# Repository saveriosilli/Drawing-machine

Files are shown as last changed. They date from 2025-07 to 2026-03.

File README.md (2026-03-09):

# Drawing Machine

This machine was designed in Fablab O Shanghai as an education project for a class called "Planet Art". The course's aim is to assemble the frame of the machine and re-design some of the structure starting from the provided design \(mainly for the laser cut plates and 3d printed accessories\) and use the machine to experience 2d/3d graphic original creations, self-expression through artwork, machine control electronics and software. After the assembly, test and familiarization with a working machine, students create artworks exploring the many possibilities of human-machine co-creation. The structure and parts of the machine is the result of many iterations and the sum of the improved design from instructors and students.

https://github.com/user-attachments/assets/3ad980b2-f0f4-412e-b6a9-14be8d8319f2

## Images

We are in the process of designing an assembly guide. Meanwhile you can refer to some images and videos to understand how the machine is assembled. Simple clue: the process is pretty easy and straightforward :\)

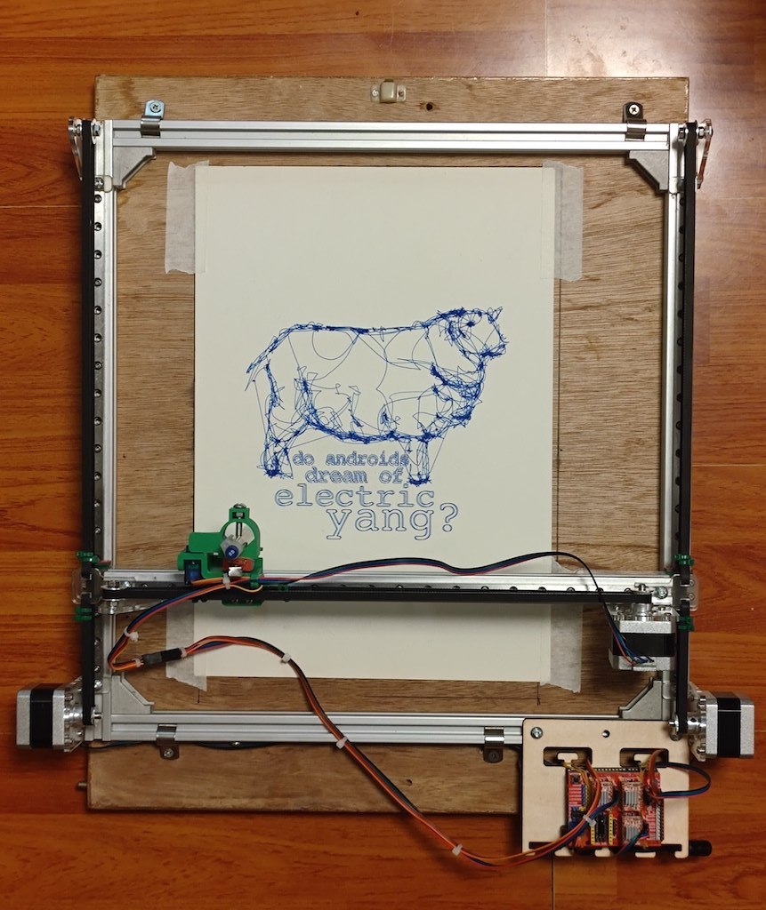
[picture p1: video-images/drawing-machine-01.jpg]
drawing machine 01


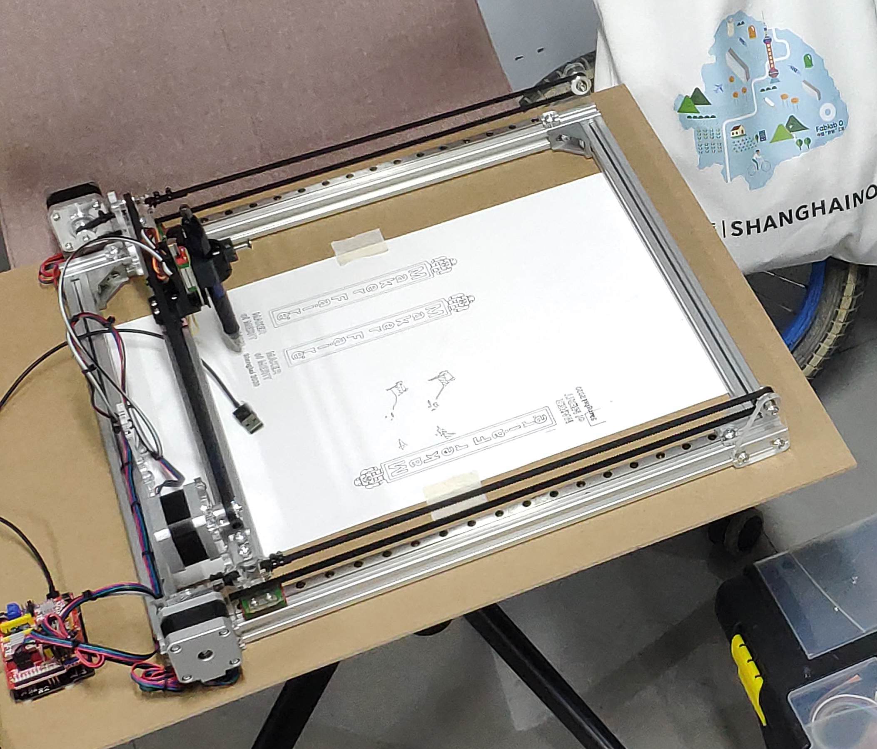
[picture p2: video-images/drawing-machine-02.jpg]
drawing machine 01


## A little history

The  structure of the machine is based on a design by **Daniele Ingrassia @satsha** for a basic machine frame to be assembled in a short workshop he gave at the **STEAM Education International Symposium of Shanghai** in 2019 organised by Fablab O Shanghai and Tongji University College of Design and Innovation. His clever and simple structure using only 20x20 aluminum frames, angle joints, t-nuts, linear guides and two laser cut parts, became part of  Fablab O Shanghai inventory and Saverio Silli @saverio used it as the base for this drawing machine.

## Highlights of this design

The machine has some notable characteristics worth mentioning:

* it can be assembled by a couple of 10 years old in less than two hours
* the 3d printed parts can be printed while assembling the structure and are ready to use when the structure is assembled
* laser cutting takes less than 5 minutes
* only a few common tools are required to assemble the structure
* the size of the machine can be customised
* pen lift is virtually free of any wobbling and can accept several types of pens and other drawing media or be customised to accept different tools

[Find all the Design files in this page](design-files/README.md)

## Machine Control

Aside from the design of the machine structure, a thorough work has been done to polish and troubleshoot the code and workflow to ensure the software installation and operation to be as straightforward as possible. A modified GRBL for Servo library is provided, and several tips are listed covering the most common solutions for a successful operation.

[Find more info on the Electronic system in this page](electronics/README.md)

The machine uses an Arduino Uno with CNC Shield and A4988 Stepper drivers with GRBL for Servo firmware. We suggest to operate the machine through Inventables' Easel.

## Bill of Materials

[Find all the BOM in this page](Material List 2022.pdf)

The material list provides links on Taobao to buy the materials and a description about the materials. For more details you can check the taobao link.

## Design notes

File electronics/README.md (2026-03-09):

# Electronics

We have included a modified and ready to use GRBL for Servo library. To install, first make sure there are no previous installation of any other GRBL libraries in your Arduino libraries folder, then just unzip and copy paste the provided folder in the Arduino Libraries folder.

Restart Arduino software and open the GRBL Upload example in the examples menu, upload the program to your Arduino Uno and the installation is complete.

## Connections

Your Arduino should be equipped with a CNC shield. Make sure the shield has:

1. all 3 jumpers under the drivers for microstepping

2. two jumpers on the Y axis duplication

3. servo motor connected as follow: brown wire \(GND\) to any GND pin on the shield, red wire \(VCC\) to any 5V pin on the shield, orange wire \(signal\) to "Endstop Z-" pin on the shield.

4. 12 Volts and 5 Amps power supply connected to the power supply connector of the CNC shield

5. Stepper motors correctly connected to the 4 pins connector next to the driver \(if motor rotate in the wrong direction, just reverse the connector

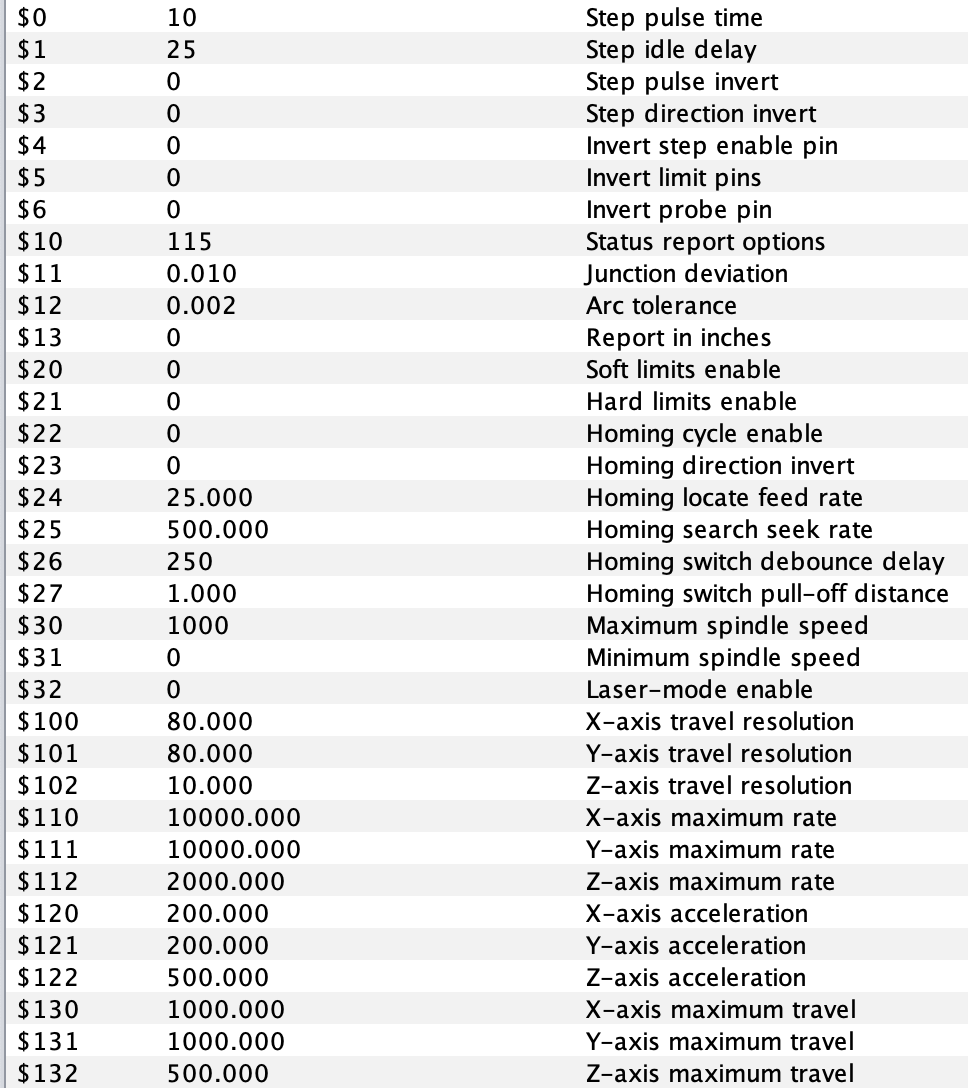
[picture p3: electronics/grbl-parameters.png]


## Notes on the servo motor operation

The basic GRBL firmware is normally controlling a _stepper_ motor to move the Z axis. This modified version make use of a _servo_ motor instead to lift the pen up and down. A normal stepper motor is controlled with coordinates coming from the G-code and its movement is expressed in millimetres  or inches. With a stepper motor you can control exactly the linear movement of the Z axis below and above the zero.

Using a **servo motor** you can only move the Z axis in two pre-defined positions: _Up \(or above the origin\) and Down \(or below the origin\)_.

Using your preferred control software \(Universal G-code Sender, Easel, eCNC to cite a few\) you will have the option to move the Z axis up and down for the length you desire, but with this modified GRBL for Servo firmware you will notice that the servo motor will only move when the machine coordinates actually pass the origin.

If your Z axis position is currently at 0mm \(the origin point\) and you move the Z axis up for 5mm, the Z axis new position will be + 5mm, _but your servo motor will not move_.

Likely, if your Z axis position is currently + 5mm and you move the Z axis down for 5mm, the Z axis new position will be 0, _but your servo motor will not move as well._

In both cases, the Z axis position was equal or bigger than zero.

On the other hand, if your Z axis position is currently at + 5mm and you move the Z axis down for 10mm, the Z axis new position will be -5mm, _and your servo motor will move once_.

**The reason is that the servo motor will only move when the Z axis position passes the origin point.** As long as it passes through the origin you will have your servo motor moving up \(from any point below 0 to any point above 0\) or moving down \(from any point above 0 to any point below 0\).

This is very important because you might find yourself clicking the Z axis movement up and down arrow several time without noticing any movement and you might believe it is a hardware problem. Instead, make sure the movements are always crossing above and below the origin point.

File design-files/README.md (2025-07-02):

# Design Files

The files included are:

1. Laser cut plates, we suggest to use 5mm acrylic. The thickness must be chosen in relation to the lenght of the screw used with t-nuts for assembly, if the thickness is too thin and the screws are too long, the screws will touch the internal channel of the aluminum frame and the plates will not be locked in place.

2. 3D printed pen lift. It is designed to use a small section of linear guide and standard slider, it can mount a standard 9g Servo Motor and it must be equipped with a rubber band to act as a spring that pushes the pen down.

3. The pen holding ring is large enough for several size of pens and markers.

4. The 3D printed parts do not require any support or brim for printing.

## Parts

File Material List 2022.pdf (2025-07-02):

1 | kits. | Kit for total
machines
NAME | TYPE | SIZE | NOTES | QUANTITY /
| | | | 1 MACHINE | QUANTITY
| | | | | / TOTAL | TAOBAO
Linear Guide / 直线导轨滑块线轨 INCLUDING SLIDER | MGN9C 标准滑块 | 350 mm | Cut to size by the
| | | vendor | 3 | 3 | https://item.taobao.com/item.htm?spm=a230r.1.999.98.cc7f523cslYHMJ&id=6001991165
| | | | | | 60&ns=1#detail
Aluminum Profile / 铝型材2020 | 2020 | 450 mm | Cut to size by the
| | | vendor | 2 | 2 | https://item.taobao.com/item.htm?spm=a1z10.5-c-s.w4002-
| | | | | | 14772119650.13.523648fe21iMTI&id=17038604486
Aluminum Profile / 铝型材2020 | 2020 | 400 mm | Cut to size by the
| | | vendor | 3 | 3 | https://item.taobao.com/item.htm?spm=a1z10.5-c-s.w4002-
| | | | | | 14772119650.13.523648fe21iMTI&id=17038604486
90° Brackets / 90度直角连接 | 2020 | | | 4 | 4 | https://item.taobao.com/item.htm?spm=2013.1.0.0.17b256e1C9TXtU&id=35207398767&s
| | | | | | ource=superboss&appId=113
T-Nuts / T型配件螺母 | 20系列-M3 | M3 | | 50 | 50 | https://item.taobao.com/item.htm?spm=a1z10.5-c-s.w4002-
| | | | | | 14772119650.27.52817ebfhoQWsb&id=17563700795
T-Nuts / T型配件螺母 | 20系列-M5 | M5 | | 30 | 30 | https://item.taobao.com/item.htm?spm=a1z10.5-c-s.w4002-
| | | | | | 14772119650.27.52817ebfhoQWsb&id=17563700795
Cap Screws: 不锈钢半圆头内六角螺丝 螺栓M3 *
8 | M3*8（100只） | M3 x 8 mm | | 50 | 50 | https://detail.tmall.com/item.htm?id=45827201018&spm=a1z09.2.0.0.5bc52e8dSysc9l&_u
| | | | | | =s2aiarg55ec3
Cap Screws: 10.9级镀锌半圆头内六角螺丝.螺栓 M5*20 | M5*20（100只） | M5 x 20
| | mm | | 20 | 20 | https://detail.tmall.com/item.htm?id=520435461948&spm=a1z09.2.0.0.5bc52e8dSysc9l&_
| | | | | | u=s2aiarg54a78
Cap Screws: 10.9级镀锌半圆头内六角螺丝.螺栓 M5*8 | M5*8（100只） | M5 x 8 mm | | 30 | 30 | https://detail.tmall.com/item.htm?id=520435461948&spm=a1z09.2.0.0.5bc52e8dSysc9l&_
| | | | | | u=s2aiarg54a78
BOLTS: 304不锈钢六角螺母 螺帽M5 M5 | M5 | 20 | 20 | https://detail.tmall.com/item.htm?id=45588511688&spm=a1z09.2.0.0.5bc52e8dSysc9l&_u
| | | | | | =s2aiarg50e7f
Acrilic sheets | any color | 400x300x4 approximate size 1 | 1
CNC Shield + Arduino + Drivers | / | / | / | 1 | 1 | https://item.taobao.com/item.htm?spm=a1z09.2.0.0.5bc52e8d0ZBPuP&id=545808938982
| | | | | | &_u=s2aiarg50a52
PULLEY (no teeth): 3D打印机配件2GT同步轮1620齿H型 皮带轮铝传动惰轮带宽电机610MM | 带宽6mm20齿-内孔5mm-
| 不带齿外径18mm | | | 3 | 3 | https://item.taobao.com/item.htm?spm=a1z09.2.0.0.5bc52e8d0ZBPuP&id=528345296400
| | | | | | &_u=s2aiarg57649
PULLEY (20 teeth): 3D打印机配件2GT同步带轮2016齿带 宽6mm内孔5 8 6.35mm传动机械轮 | 20齿-内孔5mm-高16(mm)普通 | | | 3 | 3 | https://item.taobao.com/item.htm?spm=a1z09.2.0.0.5bc52e8dSysc9l&id=523376996696&
| | | | | | _u=s2aiarg503c7
BELT: 3D打印机配件2GT同步带轮gt2皮带m xl6mm10mm橡胶带齿开口PU | GT2-
| 6MM高品质橡胶10米一卷,
| 带宽（mm）：其他 | | | 1,00 | 1 | https://item.taobao.com/item.htm?spm=a1z09.2.0.0.5bc52e8dSysc9l&id=523768456522&
| | | | | | _u=s2aiarg5ec0f
MOTOR: NEMA17 42步进电机/17hs3401/1.3A 0.30Nm/12V/雕刻机/3D打印机 | | | | 3 | 3 | https://item.taobao.com/item.htm?spm=a1z09.2.0.0.5bc52e8dSysc9l&id=595751379207&
| | | | | | _u=s2aiarg5937b
POWER SUPPLY: 液晶LED显示器 12V5A 监控开关电源适配器 水泵 灯带条12V4A 3A电 | 12V5A | | | 1,00 | 1 | https://item.taobao.com/item.htm?spm=a1z09.2.0.0.5bc52e8d0ZBPuP&id=537599507969
| | | | | | &_u=s2aiarg59675
Servo motors | SG90s blue one | | | | 1 1
MALE-TO-FEMALE WIRE
杜邦线公对母 | 公对母带胶壳/1米 | 1 | 1 | https://item.taobao.com/item.htm?spm=a1z0d.6639537.1997196601.4.4bff7484eCzNtD&i d=600371784659

Machine making workshop - Materials for

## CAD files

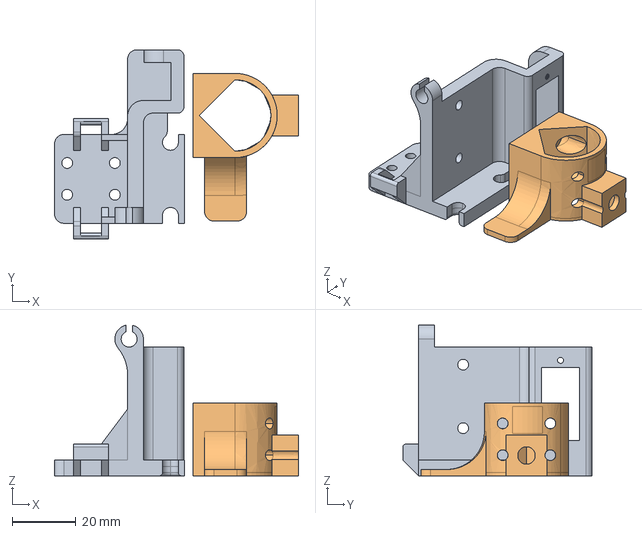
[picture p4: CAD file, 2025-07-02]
design-files/pen lift.stp
76.8 x 59.6 x 47.4 mm

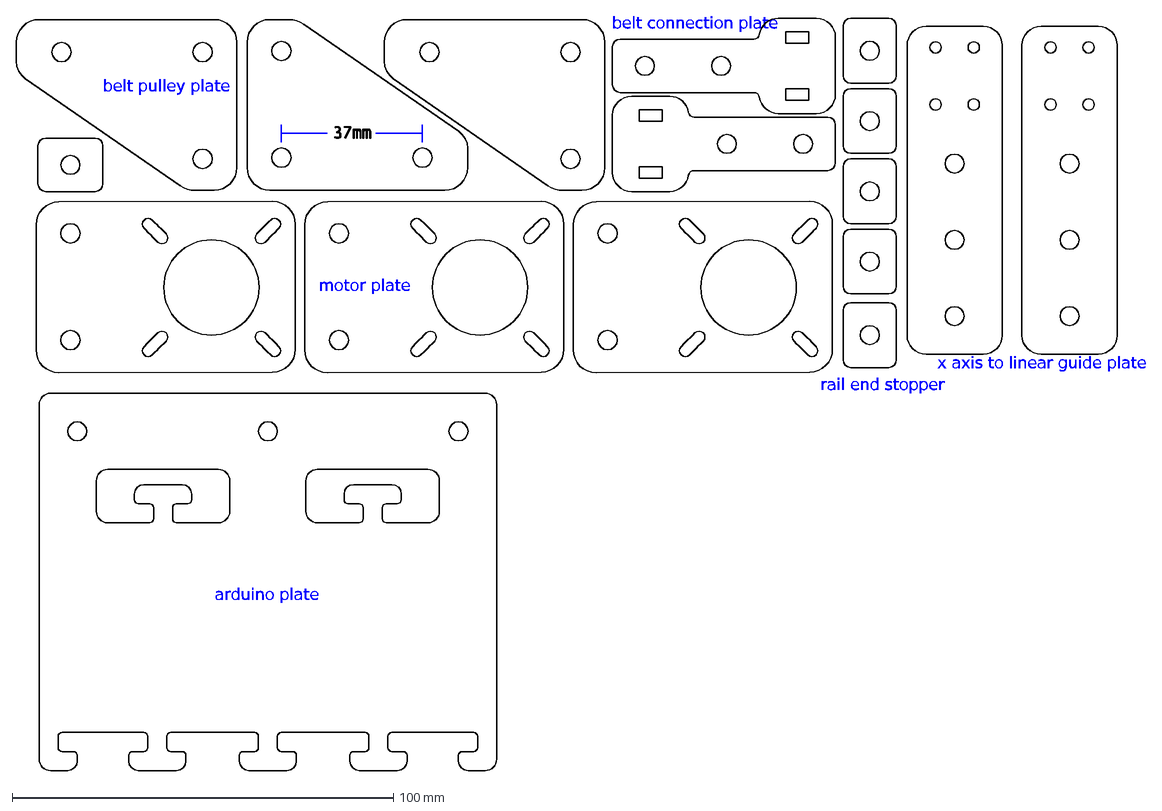
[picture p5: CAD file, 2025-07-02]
design-files/laser cut parts 5mm.dxf
x axis to linear guide plate
belt connection plate
belt pulley plate
motor plate
rail end stopper
arduino plate

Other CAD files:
design-files/laser cut parts 5mm.3dm
design-files/pen lift.3dm
design-files/pen lift.stl
